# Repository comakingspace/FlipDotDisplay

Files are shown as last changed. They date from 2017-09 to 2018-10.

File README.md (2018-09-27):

# FlipDotDisplay
3 old flip dot displays which need some work to get up and running.

They were bought at the Makerfaire Hannover 2016.

Hardware design is made in KiCAD 4.

## Function

A dot on the display is switched by magnetising an inductor, which causes the colored dot (with a small magnet embedded) to change the orientation. Because the core of the inductor stays magnetized the state of the dot is stable even without being powered.

The inductors of the pixels are hooked up in an array with 24x16. Each column is connected to a single pin of the connector and each row has two inputs; one for positive voltage and one for negative (see FlipDotSchematic). By applying a voltage to a row and a column the corresponding pixel is flipped depending on the current flow direction. The original driver probably used two different power rails and sets of transistors to change the direction of the dot. 

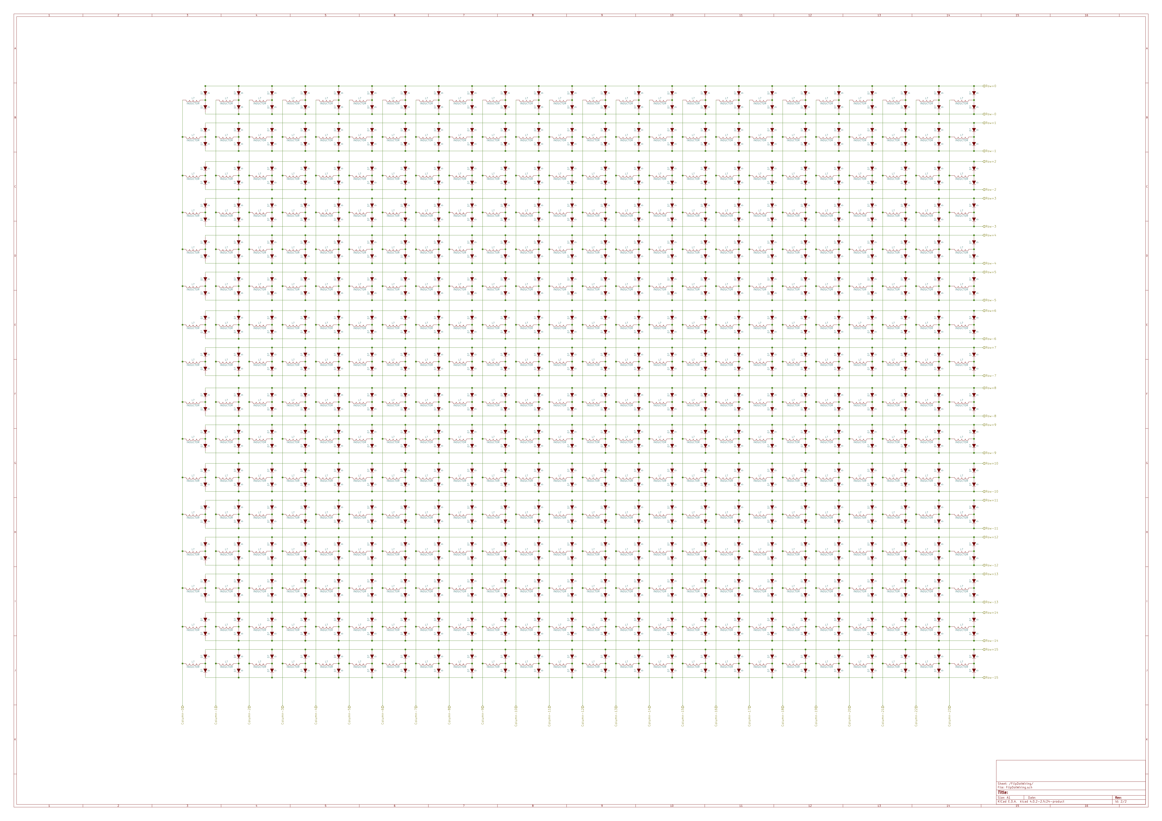
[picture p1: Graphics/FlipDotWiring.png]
Schematic of the FlipDotDisplay


The new driver will use a half-bridge configuration on each input to select the current flow direction. 

## ICs

* Half-bridge driver ICs: **L293D**
* Shift registers for output : **SN74HC595**
* Controller: **Atmega328p** (communicates via serial with the ESP8266)
* Interface for network: ESP8266 (Wemos D1 mini)

## Features

* [Adafruit GFX library](https://github.com/adafruit/Adafruit-GFX-Library) implementation
* MQTT string scroll text

## ToDo

* Pull tweets and display them (direct Hex code or text)
* Binary via MQTT
* more ?

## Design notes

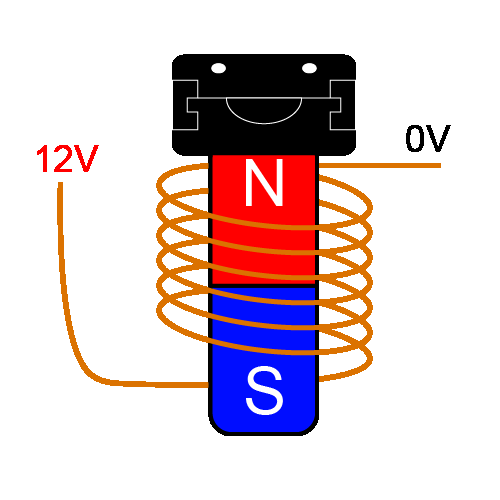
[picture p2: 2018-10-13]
Graphics/FDD_Function.gif

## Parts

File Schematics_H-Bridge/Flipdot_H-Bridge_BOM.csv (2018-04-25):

Id | Designator | Package | Quantity | Designation | Supplier and ref
1 | REF**,REF**,REF**,REF**,REF**,REF**,REF**,REF**,REF**,REF**,REF**,REF**,REF**,REF**,REF**,REF**,REF**,REF**,REF**,REF**,REF** | VIA-0.6mm | 21 | VIA-0.6mm
2 | SW1 | SW_PUSH_6mm | 1 | SW_Push
3 | P3,P2 | Pin_Header_Straight_2x08_Pitch2.54mm | 2 | CONN_02X08
4 | P1 | Pin_Header_Straight_2x13_Pitch2.54mm | 1 | CONN_02X13
5 | Y1 | Crystal_HC49-4H_Vertical | 1 | Crystal
6 | C8,C5,C1 | C_Disc_D4.7mm_W2.5mm_P5.00mm | 3 | 100nF
7 | P4 | Pin_Header_Straight_2x03_Pitch2.54mm | 1 | CONN_02X03
8 | C7,C6 | C_Disc_D4.7mm_W2.5mm_P5.00mm | 2 | 22p
9 | C2 | CP_Radial_D6.3mm_P2.50mm | 1 | 10uF
10 | D2 | LED_D3.0mm | 1 | Led_Yellow
11 | D3 | LED_D3.0mm | 1 | Led_Red
12 | D1 | LED_D3.0mm | 1 | Led_Green
13 | J1 | BARREL_JACK | 1 | Barrel_Jack
14 | C4 | CP_Radial_D6.3mm_P2.50mm | 1 | 1uF
15 | C3 | C_Disc_D4.7mm_W2.5mm_P5.00mm | 1 | 0.33uF
16 | U1,U2,U7,U8,U13 | DIP-16_W7.62mm_Socket | 5 | 74HC595
17 | U3,U4,U5,U6,U9,U10,U11,U12,U14,U15,U16,U17,U18,U19,U21,U22,U23,U24,U25,U26 | DIP-16_W7.62mm_Socket | 20 | L293D
18 | U28 | DIP-28_W7.62mm_Socket | 1 | ATMEGA328P-PU
19 | U27 | TO-220_Vertical | 1 | L7805
20 | R1 | R_Axial_DIN0204_L3.6mm_D1.6mm_P2.54mm_Vertical | 1 | 1k
21 | R2 | R_Axial_DIN0204_L3.6mm_D1.6mm_P2.54mm_Vertical | 1 | 2k
22 | R3,R4,R5 | R_Axial_DIN0204_L3.6mm_D1.6mm_P2.54mm_Vertical | 3 | 1.5K
23 | R6 | R_Axial_DIN0204_L3.6mm_D1.6mm_P2.54mm_Vertical | 1 | 10k
24 | R7 | R_Axial_DIN0204_L3.6mm_D1.6mm_P2.54mm_Vertical | 1 | 1M
25 | REF** | MountingHole_5.3mm_M5_DIN965 | 1 | MountingHole_5.3mm_M5_DIN965
26 | U20 | ESP8266_D1_Mini_cropped | 1 | ESP8266_D1_Mini
27 | G*** | FDD_Icon | 1 | LOGO

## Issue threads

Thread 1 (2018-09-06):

Special character selection doesn't yet work

Pakue95, 2018-09-06:
https://github.com/comakingspace/FlipDotDisplay/blob/ac73b9dc514dd0b5a6fa421b96d9adefe22393e7/Code/FDD-Common_Room/FDD-Common_Room.ino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

When I tired the code yesterday I got the same results as before with weird characters being displayed in place of äö etc.

NitramLegov, 2018-09-08:
https://github.com/comakingspace/FlipDotDisplay/commit/ef07109a65e885bc6020e12cc33ae8bb8f182b74 fixed this

Closed 2018-09-08.

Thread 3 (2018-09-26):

MQTT message size too short for full binary update

Pakue95, 2018-09-26:
Right now the MQTT doesn't like to send/receive more than 103 bytes. Longer messages get ignores.

NitramLegov, 2018-09-26:
The problem is within the adafruit library:
https://github.com/adafruit/Adafruit_MQTT_Library/blob/master/Adafruit_MQTT.h

It defines the maximum message length :
// how much data we save in a subscription object
// and how many subscriptions we want to be able to track.
#if defined  (__AVR_ATmega32U4__) || defined(__AVR_ATmega328P__)
  #define MAXSUBSCRIPTIONS 5
  #define SUBSCRIPTIONDATALEN 20
#else
  #define MAXSUBSCRIPTIONS 15
  #define SUBSCRIPTIONDATALEN 100
#endif

Unfortunately it is a define and not a variable. Thus, as far as I know we would have to fork the library in order to change the value.

Pakue95, 2018-09-27:
I tried increasing this value, but the limit still is present. Maybe another hard-coded max value somewhere?

Pakue95, 2018-09-27:
Someone else also has that problem. Should be fixed however...

https://github.com/adafruit/Adafruit_MQTT_Library/issues/17

Pakue95, 2018-10-14:
Might be an opportunity to change the development environment from Arduino to Espressif.

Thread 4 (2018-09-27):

BinaryTopic randomly gets triggered

Pakue95, 2018-09-27:
I noticed that the display prints out the last binary image (randomly ?) now and then. Can the MQTT server push old data?

NitramLegov, 2018-09-27:
Hmmm, in general, this should not be the case. Can you check, which QoS you are using when sending the data?
If you use another client and subscribe to the topic # you will get all messages on all topics, so you would see what the server sends.

NitramLegov, 2018-09-28:
The issue is that somebody (not looking at @Narquadah of course :D ) sent a retained message to the broker. Retained messages are explained here:
https://www.hivemq.com/blog/mqtt-essentials-part-8-retained-messages

> "A retained message is a normal MQTT message with the retained flag set to true. The broker stores the last retained message and the corresponding QoS for that topic. Each client that subscribes to a topic pattern that matches the topic of the retained message receives the retained message immediately after they subscribe. The broker stores only one retained message per topic."

In order to solve the issue, I deleted the retained message:

> "There is also a very simple way to delete the retained message of a topic: send a retained message with a zero-byte payload on the topic where you want to delete the previous retained message. The broker deletes the retained message and new subscribers no longer get a retained message for that topic. Frequently, it is not even necessary to delete, because each new retained message overwrites the previous one."

Closed 2018-10-13.

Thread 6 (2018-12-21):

MQTT client looses connection to the Broker

NitramLegov, 2018-12-21:
Unfortunately, the MQTT client looses the connection to the broker regularly.

In the broker log, you can see that the client tries to reconnect, but the broker throws an socket error.
We have two options:
1. change the mqtt library used on the client side (@Narquadah mentioned pubsubclient works for him).
Here we need to ensure the paket sizes can be adjusted. According to https://github.com/knolleary/pubsubclient/issues/110 this should work.
2. Try to debug why there is a socket error.

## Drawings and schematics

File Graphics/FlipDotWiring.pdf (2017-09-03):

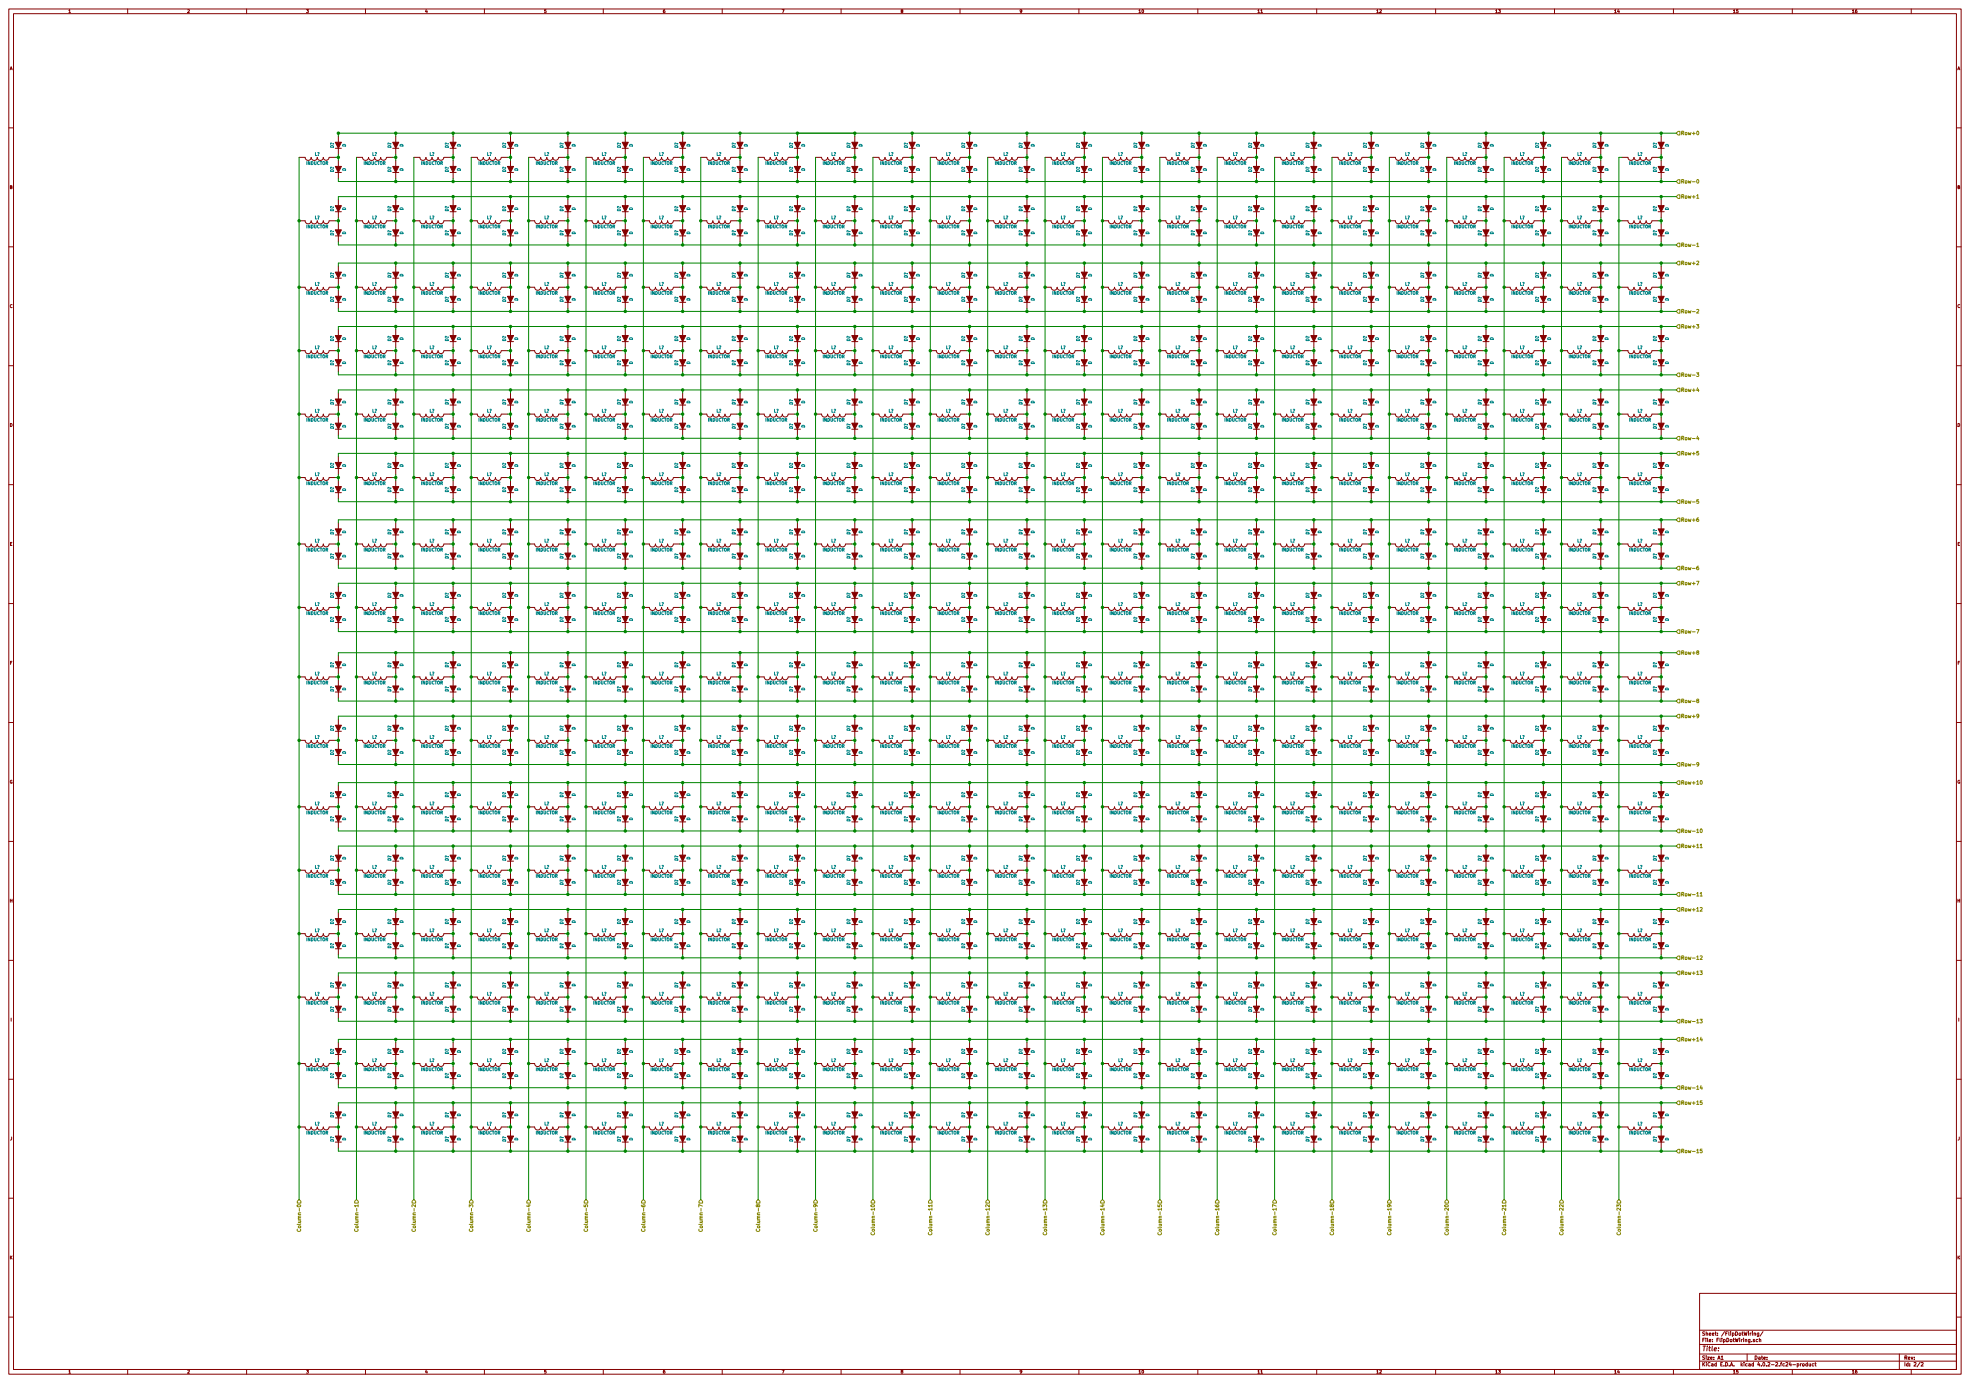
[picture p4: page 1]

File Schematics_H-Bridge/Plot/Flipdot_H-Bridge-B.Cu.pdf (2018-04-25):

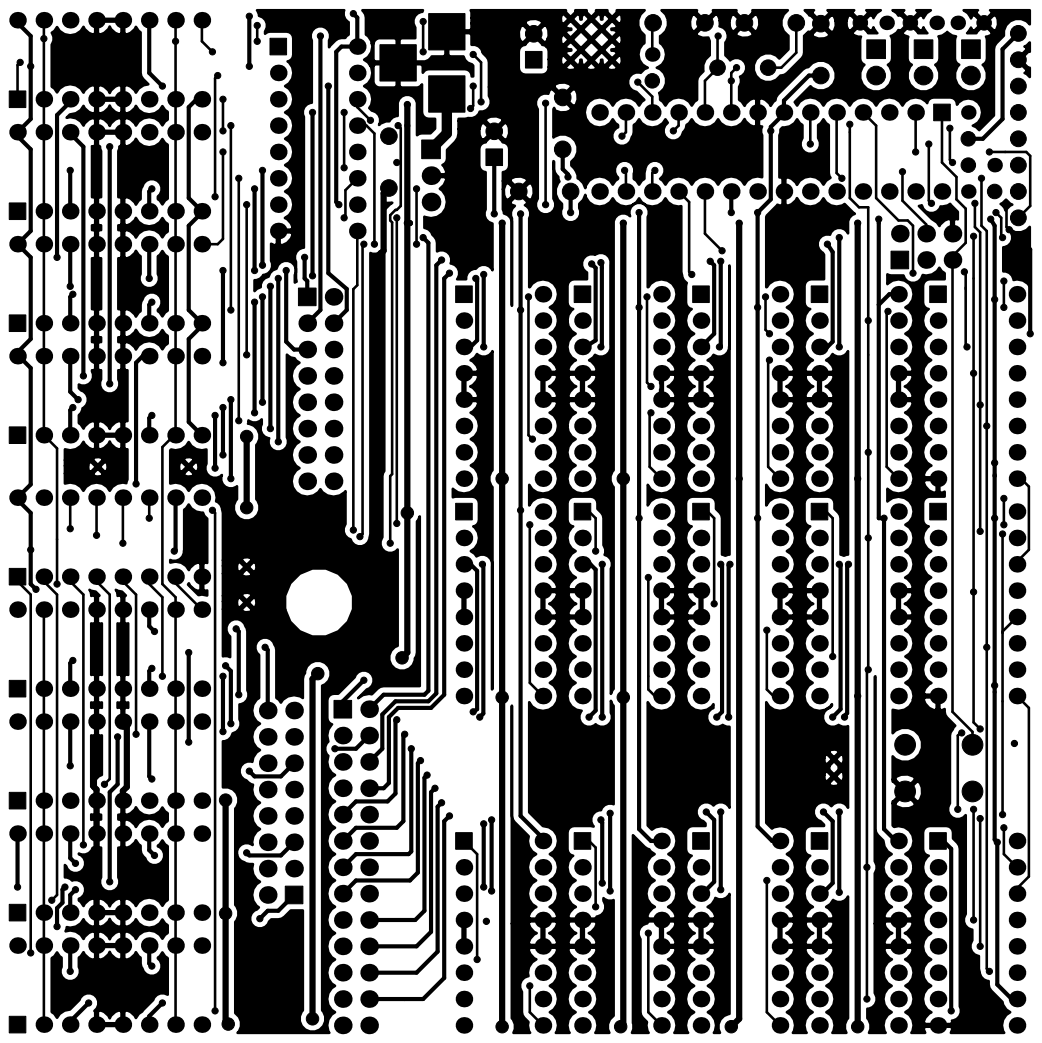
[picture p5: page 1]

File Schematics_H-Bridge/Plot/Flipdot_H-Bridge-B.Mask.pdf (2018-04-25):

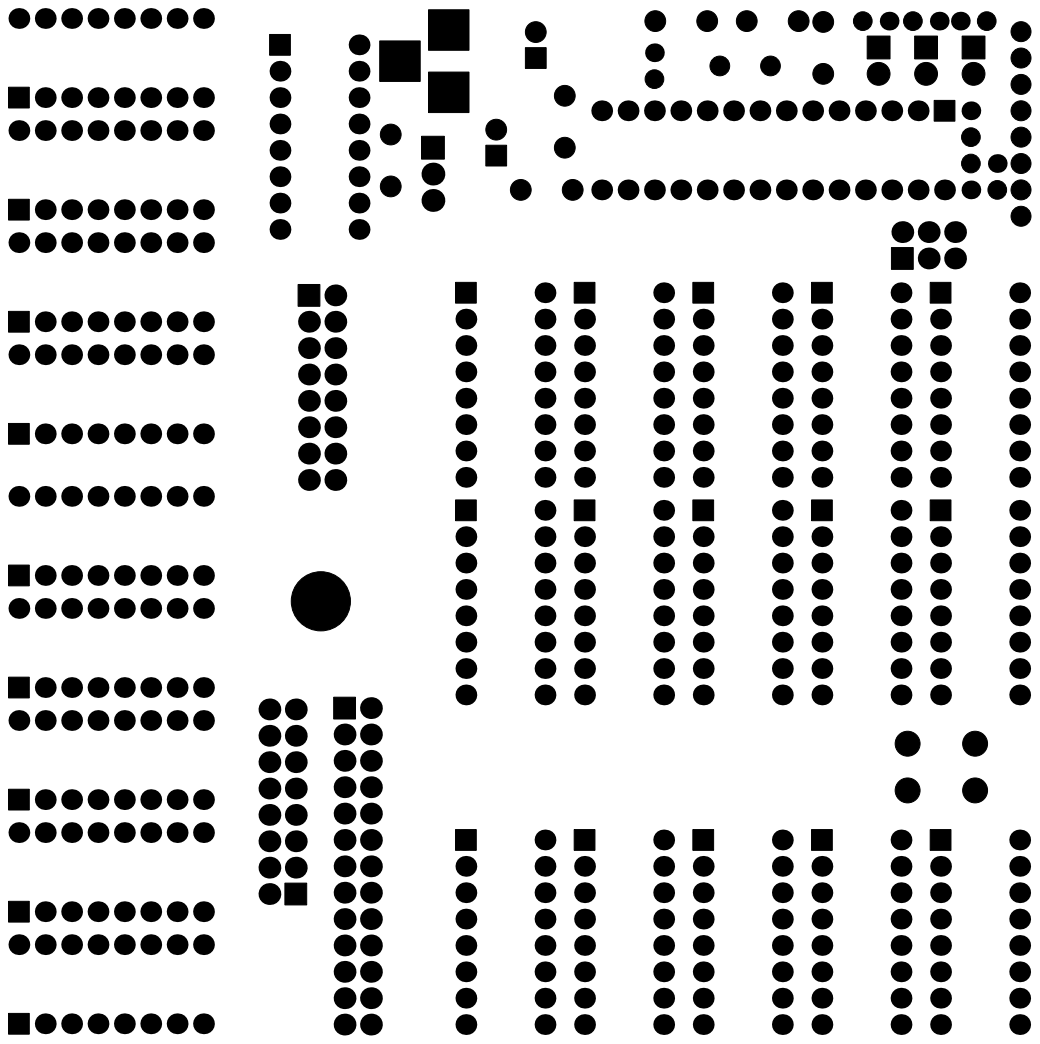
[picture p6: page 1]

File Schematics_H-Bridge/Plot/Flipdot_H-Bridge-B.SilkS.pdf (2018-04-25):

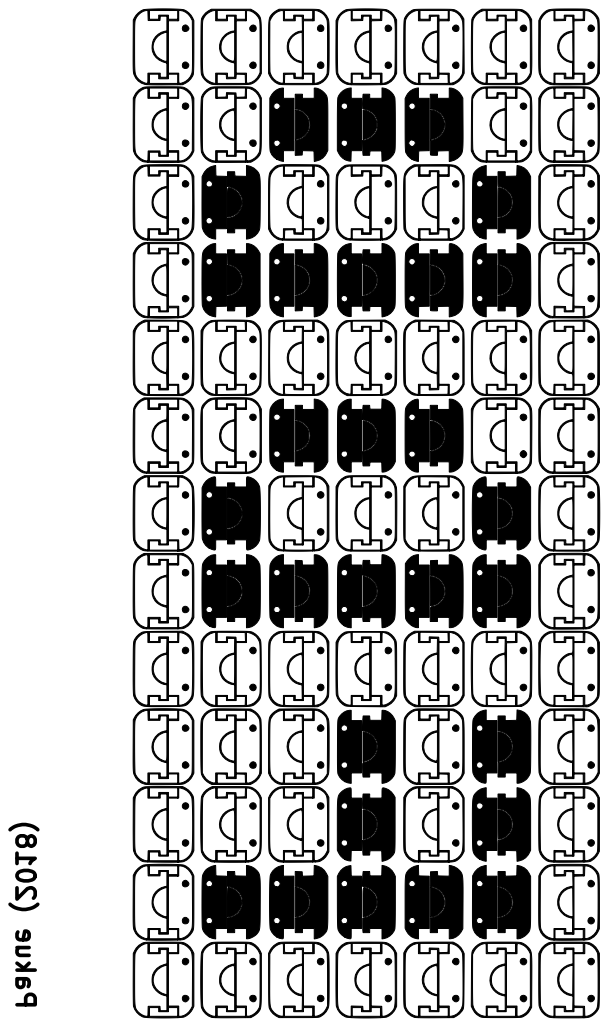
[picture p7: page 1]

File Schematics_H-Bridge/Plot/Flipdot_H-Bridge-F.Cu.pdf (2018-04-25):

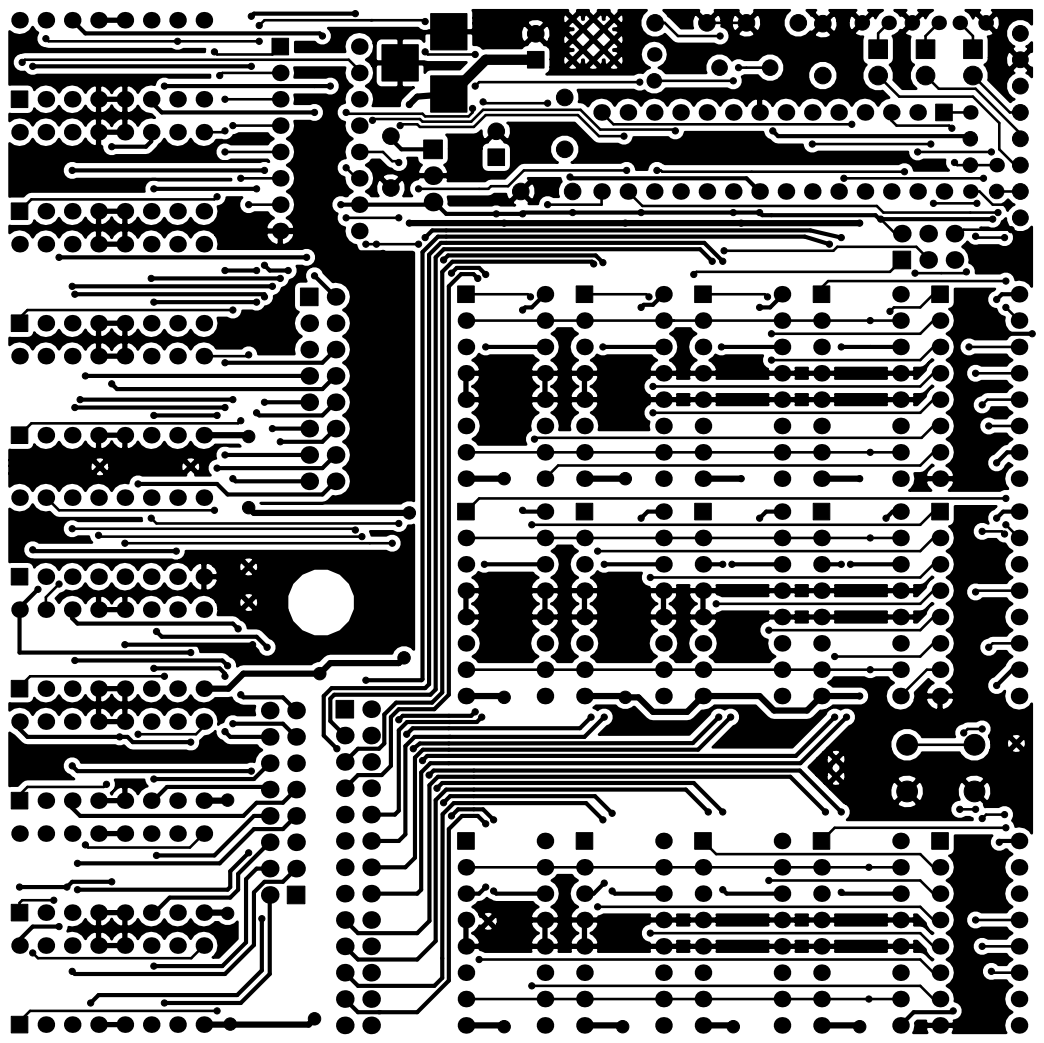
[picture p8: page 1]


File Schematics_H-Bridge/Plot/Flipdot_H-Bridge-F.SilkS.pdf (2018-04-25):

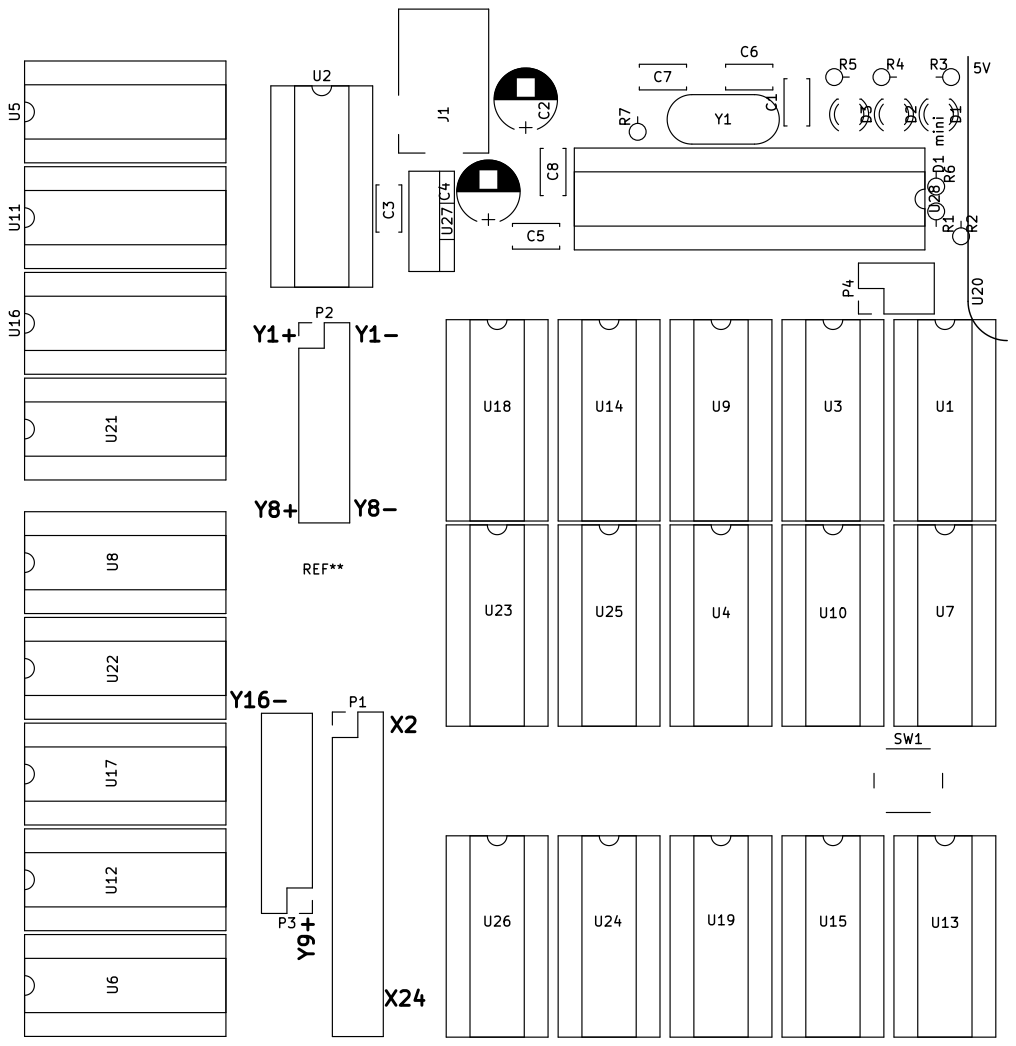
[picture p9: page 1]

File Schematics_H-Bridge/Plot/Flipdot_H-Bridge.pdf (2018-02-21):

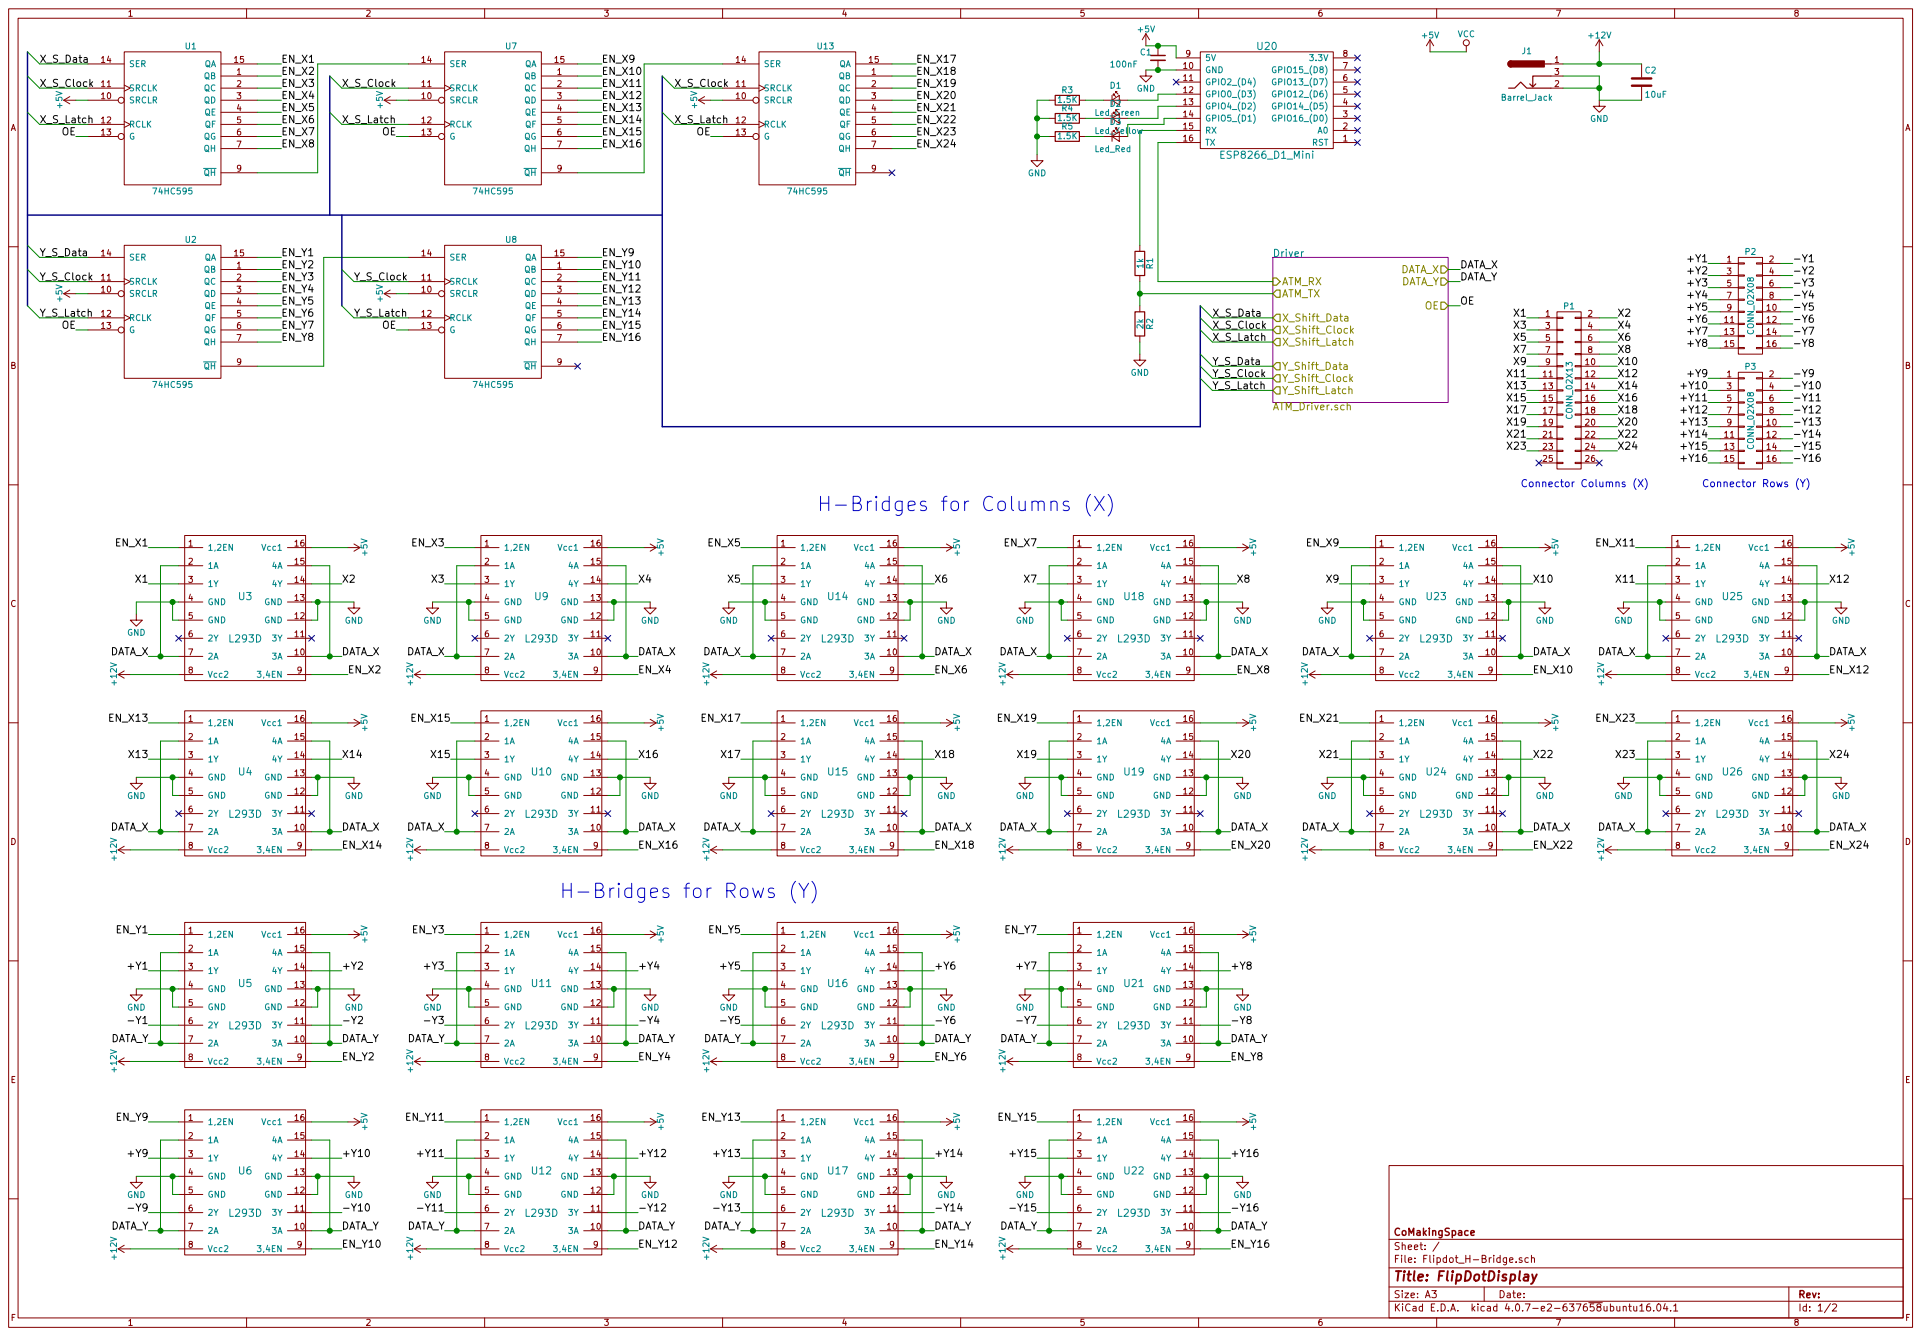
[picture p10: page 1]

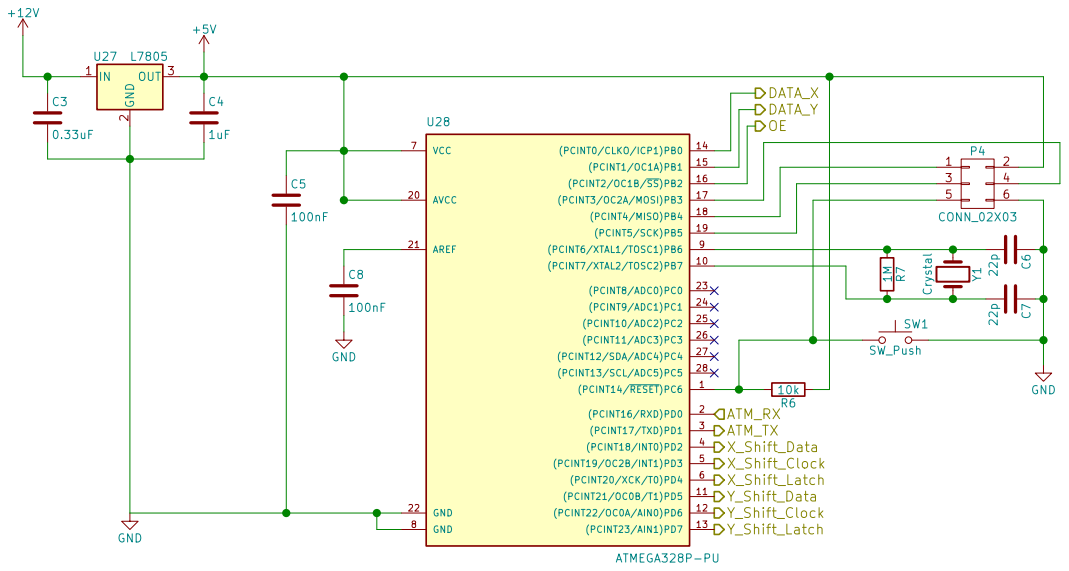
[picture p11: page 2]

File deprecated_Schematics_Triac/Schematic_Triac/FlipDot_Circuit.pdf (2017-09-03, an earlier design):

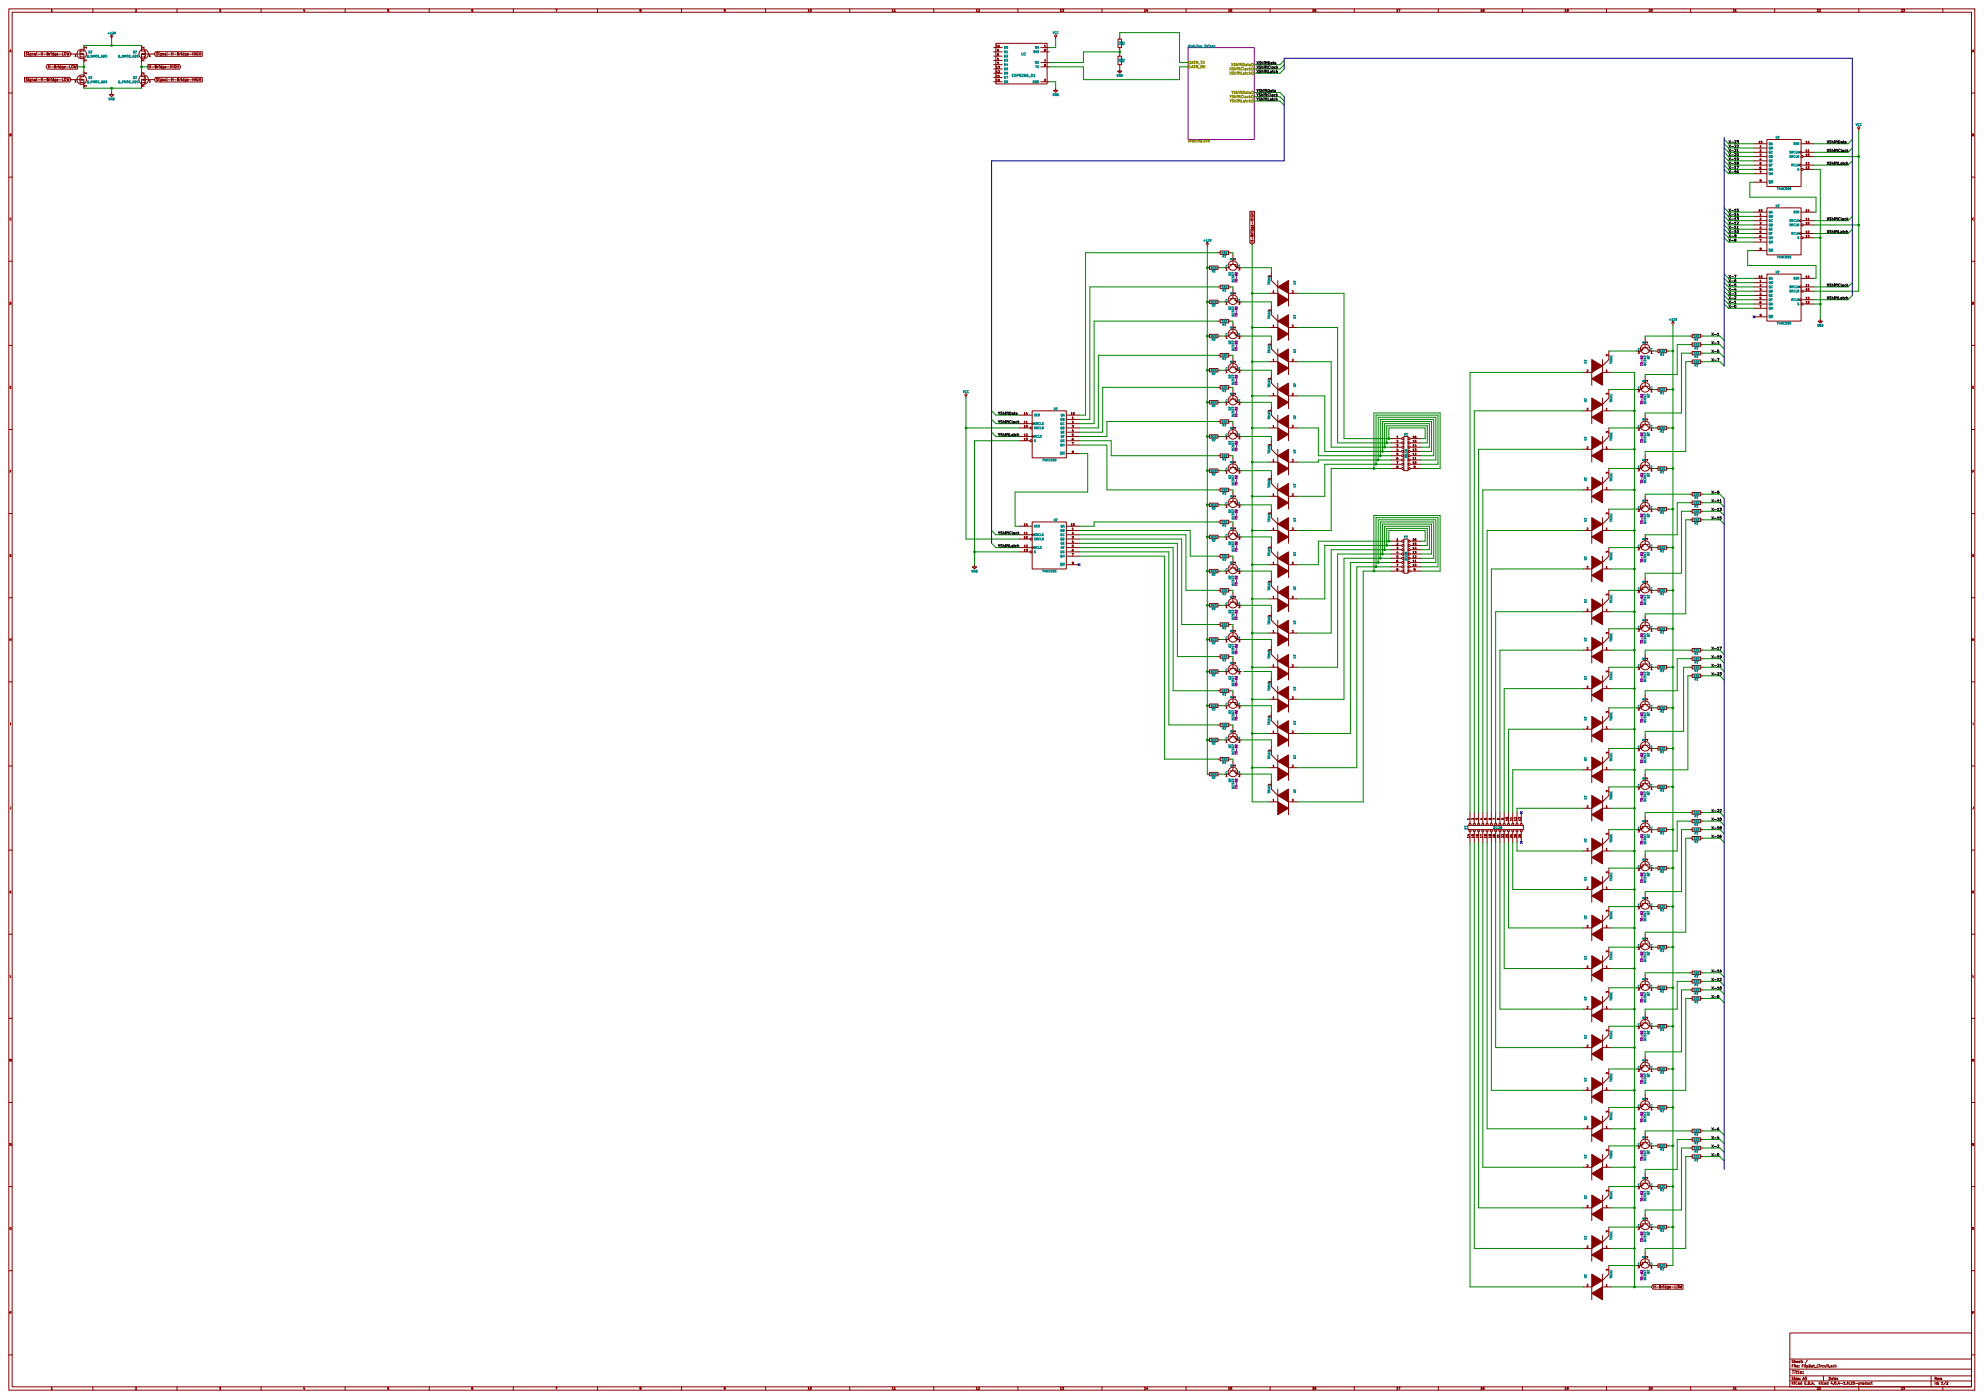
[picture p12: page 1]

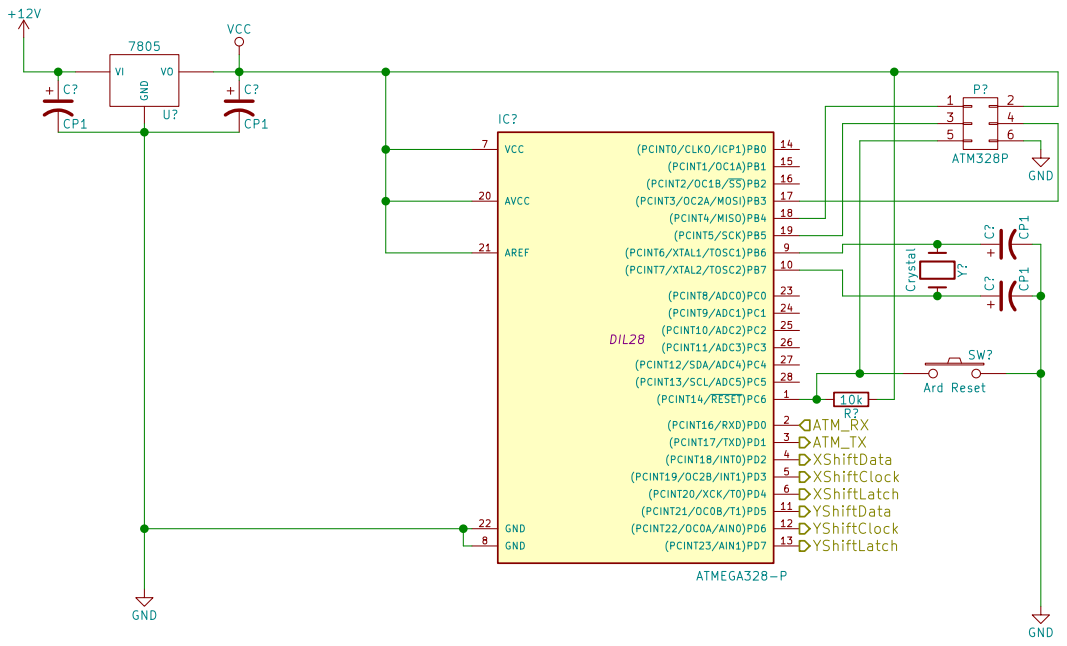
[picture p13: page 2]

Id: 2/2 Title: File: Arduino.sch Sheet: /Arduino_Driver/

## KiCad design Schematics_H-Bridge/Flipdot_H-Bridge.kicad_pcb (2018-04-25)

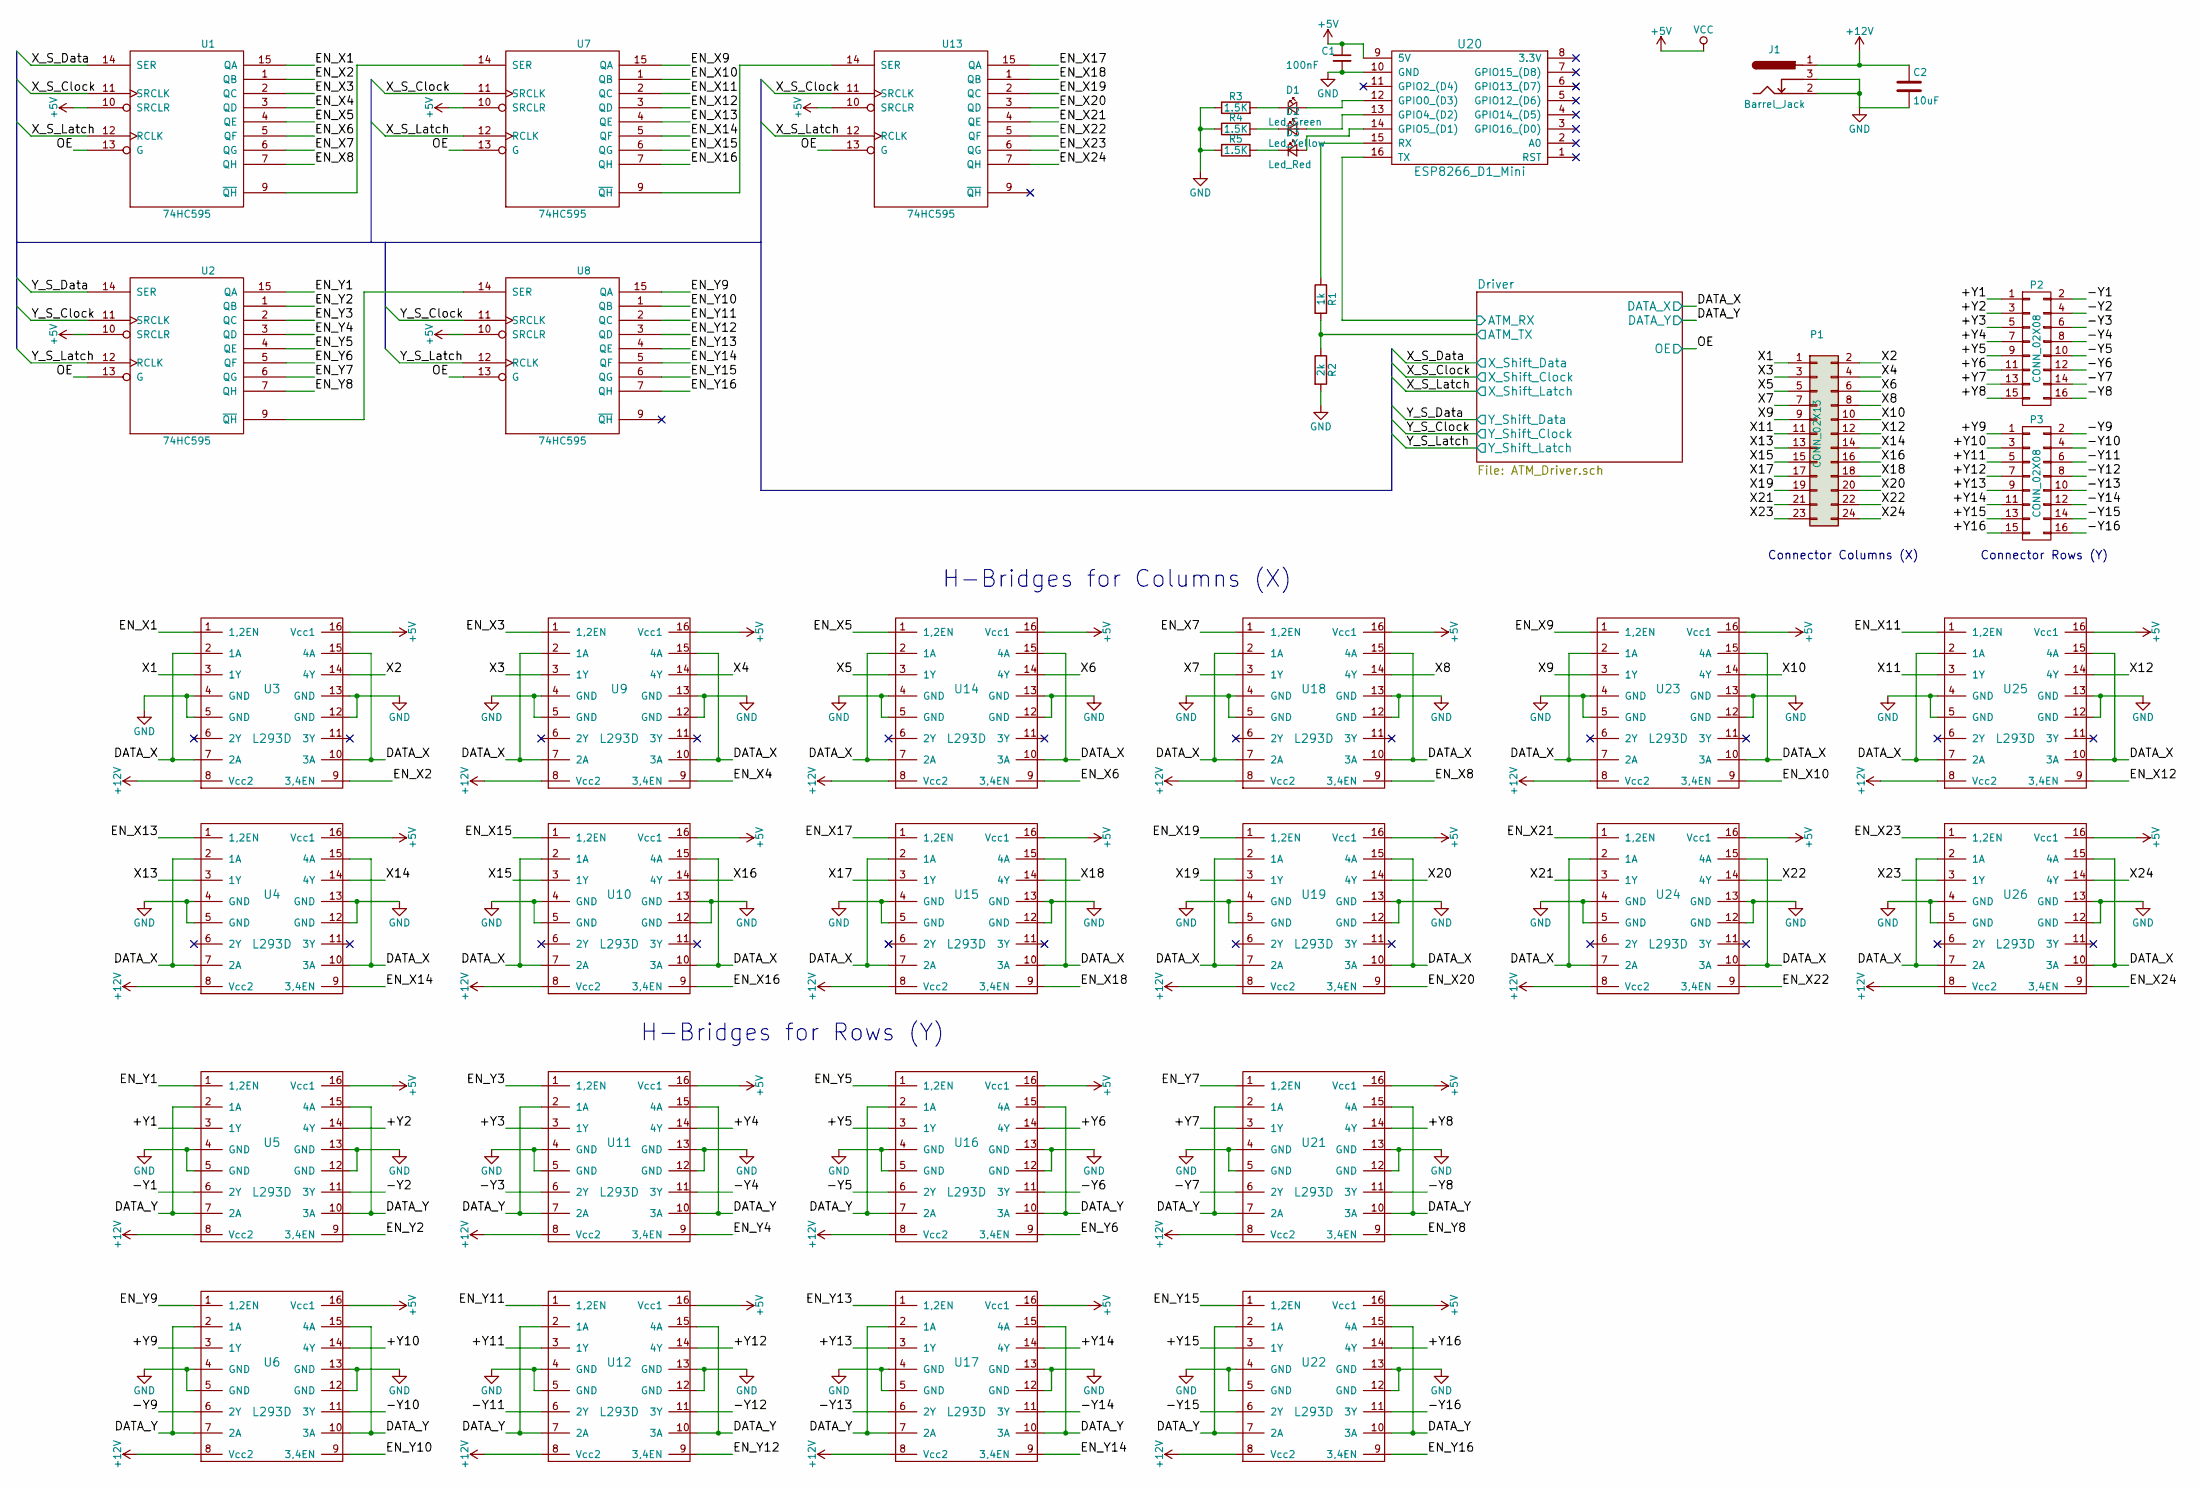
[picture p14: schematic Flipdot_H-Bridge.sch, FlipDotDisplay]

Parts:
C1: 100nF; C_Disc_D4.7mm_W2.5mm_P5.00mm
C2: 10uF; CP_Radial_D6.3mm_P2.50mm
D1: Led_Green; LED_D3.0mm
D2: Led_Yellow; LED_D3.0mm
D3: Led_Red; LED_D3.0mm
J1: Barrel_Jack; BARREL_JACK
P1: CONN_02X13; Pin_Header_Straight_2x13_Pitch2.54mm
P2, P3: CONN_02X08; Pin_Header_Straight_2x08_Pitch2.54mm
R1: 1k; R_Axial_DIN0204_L3.6mm_D1.6mm_P2.54mm_Vertical
R2: 2k; R_Axial_DIN0204_L3.6mm_D1.6mm_P2.54mm_Vertical
R3, R4, R5: 1.5K; R_Axial_DIN0204_L3.6mm_D1.6mm_P2.54mm_Vertical
U1, U2, U7, U8, U13: 74HC595; DIP-16_W7.62mm_Socket
U3, U4, U5, U6, U9, U10, U11, U12, U14, U15, U16, U17, U18, U19, U21, U22, U23, U24, U25, U26: L293D; DIP-16_W7.62mm_Socket
U20: ESP8266_D1_Mini

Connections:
+5V: C1.1, U1.10 (SRCLR), U1.16 (VCC), U2.10 (SRCLR), U2.16 (VCC), U3.16 (Vcc1), U4.16 (Vcc1), U5.16 (Vcc1), U6.16 (Vcc1), U7.10 (SRCLR), U7.16 (VCC), U8.10 (SRCLR), U8.16 (VCC), U9.16 (Vcc1), U10.16 (Vcc1), U11.16 (Vcc1), U12.16 (Vcc1), U13.10 (SRCLR), U13.16 (VCC), U14.16 (Vcc1), U15.16 (Vcc1), U16.16 (Vcc1), U17.16 (Vcc1), U18.16 (Vcc1), U19.16 (Vcc1), U20.9 (5V), U21.16 (Vcc1), U22.16 (Vcc1), U23.16 (Vcc1), U24.16 (Vcc1), U25.16 (Vcc1), U26.16 (Vcc1); also elsewhere on the board
+12V: C2.1, J1.1, U3.8 (Vcc2), U4.8 (Vcc2), U5.8 (Vcc2), U6.8 (Vcc2), U9.8 (Vcc2), U10.8 (Vcc2), U11.8 (Vcc2), U12.8 (Vcc2), U14.8 (Vcc2), U15.8 (Vcc2), U16.8 (Vcc2), U17.8 (Vcc2), U18.8 (Vcc2), U19.8 (Vcc2), U21.8 (Vcc2), U22.8 (Vcc2), U23.8 (Vcc2), U24.8 (Vcc2), U25.8 (Vcc2), U26.8 (Vcc2); also elsewhere on the board
/+Y1: P2.1, U5.3 (1Y)
/+Y2: P2.3, U5.14 (4Y)
/+Y3: P2.5, U11.3 (1Y)
/+Y4: P2.7, U11.14 (4Y)
/+Y5: P2.9, U16.3 (1Y)
/+Y6: P2.11, U16.14 (4Y)
/+Y7: P2.13, U21.3 (1Y)
/+Y8: P2.15, U21.14 (4Y)
/+Y9: P3.1, U6.3 (1Y)
/+Y10: P3.3, U6.14 (4Y)
/+Y11: P3.5, U12.3 (1Y)
/+Y12: P3.7, U12.14 (4Y)
/+Y13: P3.9, U17.3 (1Y)
/+Y14: P3.11, U17.14 (4Y)
/+Y15: P3.13, U22.3 (1Y)
/+Y16: P3.15, U22.14 (4Y)
/-Y1: P2.2, U5.6 (2Y)
/-Y2: P2.4, U5.11 (3Y)
/-Y3: P2.6, U11.6 (2Y)
/-Y4: P2.8, U11.11 (3Y)
/-Y5: P2.10, U16.6 (2Y)
/-Y6: P2.12, U16.11 (3Y)
/-Y7: P2.14, U21.6 (2Y)
/-Y8: P2.16, U21.11 (3Y)
/-Y9: P3.2, U6.6 (2Y)
/-Y10: P3.4, U6.11 (3Y)
/-Y11: P3.6, U12.6 (2Y)
/-Y12: P3.8, U12.11 (3Y)
/-Y13: P3.10, U17.6 (2Y)
/-Y14: P3.12, U17.11 (3Y)
/-Y15: P3.14, U22.6 (2Y)
/-Y16: P3.16, U22.11 (3Y)
/DATA_X: U3.2 (1A), U3.7 (2A), U3.10 (3A), U3.15 (4A), U4.2 (1A), U4.7 (2A), U4.10 (3A), U4.15 (4A), U9.2 (1A), U9.7 (2A), U9.10 (3A), U9.15 (4A), U10.2 (1A), U10.7 (2A), U10.10 (3A), U10.15 (4A), U14.2 (1A), U14.7 (2A), U14.10 (3A), U14.15 (4A), U15.2 (1A), U15.7 (2A), U15.10 (3A), U15.15 (4A), U18.2 (1A), U18.7 (2A), U18.10 (3A), U18.15 (4A), U19.2 (1A), U19.7 (2A), U19.10 (3A), U19.15 (4A), U23.2 (1A), U23.7 (2A), U23.10 (3A), U23.15 (4A), U24.2 (1A), U24.7 (2A), U24.10 (3A), U24.15 (4A), U25.2 (1A), U25.7 (2A), U25.10 (3A), U25.15 (4A), U26.2 (1A), U26.7 (2A), U26.10 (3A), U26.15 (4A); also elsewhere on the board
/DATA_Y: U5.2 (1A), U5.7 (2A), U5.10 (3A), U5.15 (4A), U6.2 (1A), U6.7 (2A), U6.10 (3A), U6.15 (4A), U11.2 (1A), U11.7 (2A), U11.10 (3A), U11.15 (4A), U12.2 (1A), U12.7 (2A), U12.10 (3A), U12.15 (4A), U16.2 (1A), U16.7 (2A), U16.10 (3A), U16.15 (4A), U17.2 (1A), U17.7 (2A), U17.10 (3A), U17.15 (4A), U21.2 (1A), U21.7 (2A), U21.10 (3A), U21.15 (4A), U22.2 (1A), U22.7 (2A), U22.10 (3A), U22.15 (4A); also elsewhere on the board
/Driver/ATM_RX: U20.16 (TX); also elsewhere on the board
/Driver/ATM_TX: R1.2, R2.1; also elsewhere on the board
/EN_X1: U1.15 (QA), U3.1 (1,2EN)
/EN_X2: U1.1 (QB), U3.9 (3,4EN)
/EN_X3: U1.2 (QC), U9.1 (1,2EN)
/EN_X4: U1.3 (QD), U9.9 (3,4EN)
/EN_X5: U1.4 (QE), U14.1 (1,2EN)
/EN_X6: U1.5 (QF), U14.9 (3,4EN)
/EN_X7: U1.6 (QG), U18.1 (1,2EN)
/EN_X8: U1.7 (QH), U18.9 (3,4EN)
/EN_X9: U7.15 (QA), U23.1 (1,2EN)
/EN_X10: U7.1 (QB), U23.9 (3,4EN)
/EN_X11: U7.2 (QC), U25.1 (1,2EN)
/EN_X12: U7.3 (QD), U25.9 (3,4EN)
/EN_X13: U4.1 (1,2EN), U7.4 (QE)
/EN_X14: U4.9 (3,4EN), U7.5 (QF)
/EN_X15: U7.6 (QG), U10.1 (1,2EN)
/EN_X16: U7.7 (QH), U10.9 (3,4EN)
/EN_X17: U13.15 (QA), U15.1 (1,2EN)
/EN_X18: U13.1 (QB), U15.9 (3,4EN)
/EN_X19: U13.2 (QC), U19.1 (1,2EN)
/EN_X20: U13.3 (QD), U19.9 (3,4EN)
/EN_X21: U13.4 (QE), U24.1 (1,2EN)
/EN_X22: U13.5 (QF), U24.9 (3,4EN)
/EN_X23: U13.6 (QG), U26.1 (1,2EN)
/EN_X24: U13.7 (QH), U26.9 (3,4EN)
/EN_Y1: U2.15 (QA), U5.1 (1,2EN)
/EN_Y2: U2.1 (QB), U5.9 (3,4EN)
/EN_Y3: U2.2 (QC), U11.1 (1,2EN)
/EN_Y4: U2.3 (QD), U11.9 (3,4EN)
/EN_Y5: U2.4 (QE), U16.1 (1,2EN)
/EN_Y6: U2.5 (QF), U16.9 (3,4EN)
/EN_Y7: U2.6 (QG), U21.1 (1,2EN)
/EN_Y8: U2.7 (QH), U21.9 (3,4EN)
/EN_Y9: U6.1 (1,2EN), U8.15 (QA)
/EN_Y10: U6.9 (3,4EN), U8.1 (QB)
/EN_Y11: U8.2 (QC), U12.1 (1,2EN)
/EN_Y12: U8.3 (QD), U12.9 (3,4EN)
/EN_Y13: U8.4 (QE), U17.1 (1,2EN)
/EN_Y14: U8.5 (QF), U17.9 (3,4EN)
/EN_Y15: U8.6 (QG), U22.1 (1,2EN)
/EN_Y16: U8.7 (QH), U22.9 (3,4EN)
/OE: U1.13 (G), U2.13 (G), U7.13 (G), U8.13 (G), U13.13 (G); also elsewhere on the board
/X1: P1.1, U3.3 (1Y)
/X2: P1.2, U3.14 (4Y)
/X3: P1.3, U9.3 (1Y)
/X4: P1.4, U9.14 (4Y)
/X5: P1.5, U14.3 (1Y)
/X6: P1.6, U14.14 (4Y)
/X7: P1.7, U18.3 (1Y)
/X8: P1.8, U18.14 (4Y)
/X9: P1.9, U23.3 (1Y)
/X10: P1.10, U23.14 (4Y)
/X11: P1.11, U25.3 (1Y)
/X12: P1.12, U25.14 (4Y)
/X13: P1.13, U4.3 (1Y)
/X14: P1.14, U4.14 (4Y)
/X15: P1.15, U10.3 (1Y)
/X16: P1.16, U10.14 (4Y)
/X17: P1.17, U15.3 (1Y)
/X18: P1.18, U15.14 (4Y)
/X19: P1.19, U19.3 (1Y)
/X20: P1.20, U19.14 (4Y)
/X21: P1.21, U24.3 (1Y)
/X22: P1.22, U24.14 (4Y)
/X23: P1.23, U26.3 (1Y)
/X24: P1.24, U26.14 (4Y)
/X_S_Clock: U1.11 (SRCLK), U7.11 (SRCLK), U13.11 (SRCLK); also elsewhere on the board
/X_S_Data: U1.14 (SER); also elsewhere on the board
/X_S_Latch: U1.12 (RCLK), U7.12 (RCLK), U13.12 (RCLK); also elsewhere on the board
/Y_S_Clock: U2.11 (SRCLK), U8.11 (SRCLK); also elsewhere on the board
/Y_S_Data: U2.14 (SER); also elsewhere on the board
/Y_S_Latch: U2.12 (RCLK), U8.12 (RCLK); also elsewhere on the board
GND: C1.2, C2.2, J1.2, J1.3, R2.2, R3.1, R4.1, R5.1, U1.8 (GND), U2.8 (GND), U3.4 (GND), U3.5 (GND), U3.12 (GND), U3.13 (GND), U4.4 (GND), U4.5 (GND), U4.12 (GND), U4.13 (GND), U5.4 (GND), U5.5 (GND), U5.12 (GND), U5.13 (GND), U6.4 (GND), U6.5 (GND), U6.12 (GND), U6.13 (GND), U7.8 (GND), U8.8 (GND), U9.4 (GND), U9.5 (GND), U9.12 (GND), U9.13 (GND), U10.4 (GND), U10.5 (GND), U10.12 (GND), U10.13 (GND), U11.4 (GND), U11.5 (GND), U11.12 (GND), U11.13 (GND), U12.4 (GND), U12.5 (GND), U12.12 (GND), U12.13 (GND), U13.8 (GND), U14.4 (GND), U14.5 (GND), U14.12 (GND), U14.13 (GND), U15.4 (GND), U15.5 (GND), U15.12 (GND), U15.13 (GND), U16.4 (GND), U16.5 (GND), U16.12 (GND), U16.13 (GND), U17.4 (GND), U17.5 (GND), U17.12 (GND), U17.13 (GND), U18.4 (GND), U18.5 (GND), U18.12 (GND), U18.13 (GND), U19.4 (GND), U19.5 (GND), U19.12 (GND), U19.13 (GND), U20.10 (GND), U21.4 (GND), U21.5 (GND), U21.12 (GND), U21.13 (GND), U22.4 (GND), U22.5 (GND), U22.12 (GND), U22.13 (GND), U23.4 (GND), U23.5 (GND), U23.12 (GND), U23.13 (GND), U24.4 (GND), U24.5 (GND), U24.12 (GND), U24.13 (GND), U25.4 (GND), U25.5 (GND), U25.12 (GND), U25.13 (GND), U26.4 (GND), U26.5 (GND), U26.12 (GND), U26.13 (GND); also elsewhere on the board
unnamed: D1.1 (K), R3.2
unnamed: D1.2 (A), U20.12 (GPIO0_(D3))
unnamed: D2.1 (K), R4.2
unnamed: D2.2 (A), U20.13 (GPIO4_(D2))
unnamed: D3.1 (K), R5.2
unnamed: D3.2 (A), U20.14 (GPIO5_(D1))
unnamed: R1.1, U20.15 (RX)
unnamed: U1.9 (~QH), U7.14 (SER)
unnamed: U2.9 (~QH), U8.14 (SER)
unnamed: U7.9 (~QH), U13.14 (SER)

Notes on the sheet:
Connector Columns (X)
Connector Rows (Y)
H-Bridges for Rows (Y)
H-Bridges for Columns (X)

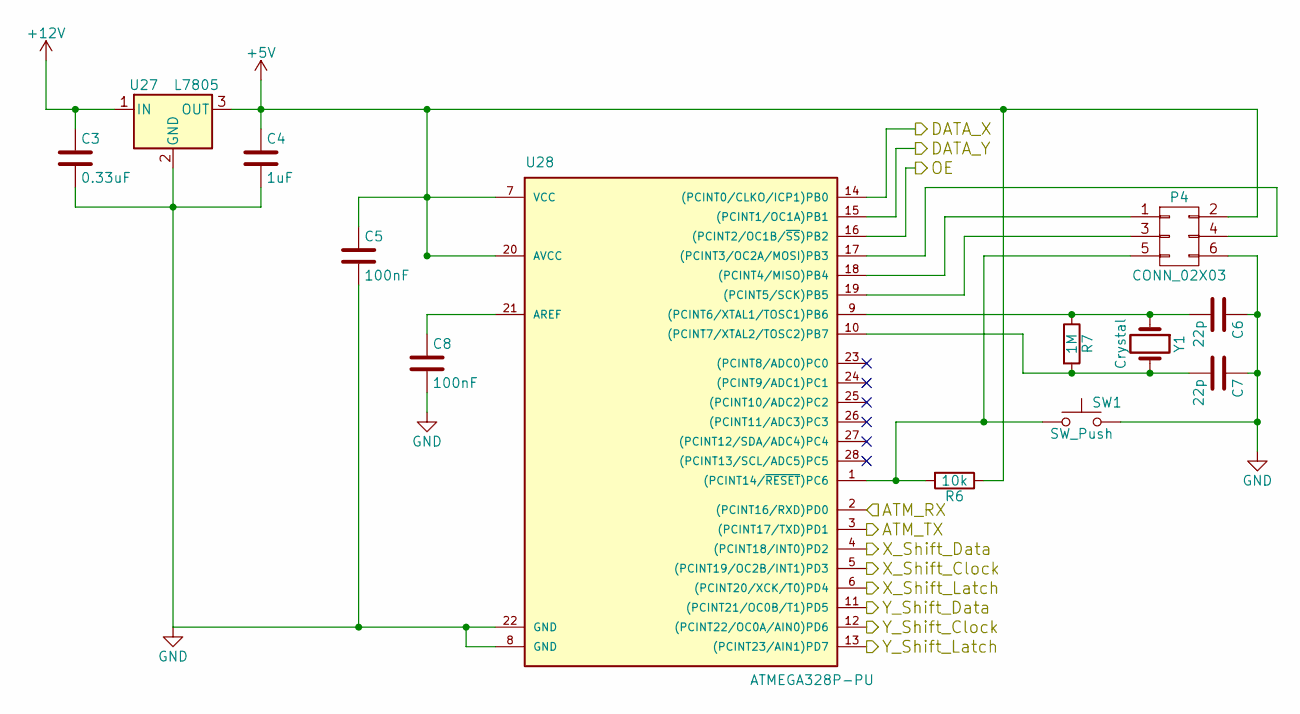
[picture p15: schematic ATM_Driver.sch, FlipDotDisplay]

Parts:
C3: 0.33uF; C_Disc_D4.7mm_W2.5mm_P5.00mm
C4: 1uF; CP_Radial_D6.3mm_P2.50mm
C5, C8: 100nF; C_Disc_D4.7mm_W2.5mm_P5.00mm
C6, C7: 22p; C_Disc_D4.7mm_W2.5mm_P5.00mm
P4: CONN_02X03; Pin_Header_Straight_2x03_Pitch2.54mm
R6: 10k; R_Axial_DIN0204_L3.6mm_D1.6mm_P2.54mm_Vertical
R7: 1M; R_Axial_DIN0204_L3.6mm_D1.6mm_P2.54mm_Vertical
SW1: SW_Push; SW_PUSH_6mm
U27: L7805; TO-220_Vertical
U28: ATMEGA328P-PU; DIP-28_W7.62mm_Socket
Y1: Crystal; Crystal_HC49-4H_Vertical

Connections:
+5V: C4.1, C5.1, P4.2, R6.1, U27.3 (OUT), U28.7 (VCC), U28.20 (AVCC); also elsewhere on the board
+12V: C3.1, U27.1 (IN); also elsewhere on the board
/DATA_X: U28.14 ((PCINT0/CLKO/ICP1)PB0); also elsewhere on the board
/DATA_Y: U28.15 ((PCINT1/OC1A)PB1); also elsewhere on the board
/Driver/ATM_RX: U28.2 ((PCINT16/RXD)PD0); also elsewhere on the board
/Driver/ATM_TX: U28.3 ((PCINT17/TXD)PD1); also elsewhere on the board
/OE: U28.16 ((PCINT2/OC1B/~SS~)PB2); also elsewhere on the board
/X_S_Clock: U28.5 ((PCINT19/OC2B/INT1)PD3); also elsewhere on the board
/X_S_Data: U28.4 ((PCINT18/INT0)PD2); also elsewhere on the board
/X_S_Latch: U28.6 ((PCINT20/XCK/T0)PD4); also elsewhere on the board
/Y_S_Clock: U28.12 ((PCINT22/OC0A/AIN0)PD6); also elsewhere on the board
/Y_S_Data: U28.11 ((PCINT21/OC0B/T1)PD5); also elsewhere on the board
/Y_S_Latch: U28.13 ((PCINT23/AIN1)PD7); also elsewhere on the board
GND: C3.2, C4.2, C5.2, C6.1, C7.1, C8.2, P4.6, SW1.2, U27.2 (GND), U28.8 (GND), U28.22 (GND); also elsewhere on the board
unnamed: C6.2, R7.1, U28.9 ((PCINT6/XTAL1/TOSC1)PB6), Y1.1
unnamed: C7.2, R7.2, U28.10 ((PCINT7/XTAL2/TOSC2)PB7), Y1.2
unnamed: C8.1, U28.21 (AREF)
unnamed: P4.1, U28.18 ((PCINT4/MISO)PB4)
unnamed: P4.3, U28.19 ((PCINT5/SCK)PB5)
unnamed: P4.4, U28.17 ((PCINT3/OC2A/MOSI)PB3)
unnamed: P4.5, R6.2, SW1.1, U28.1 ((PCINT14/~RESET~)PC6)

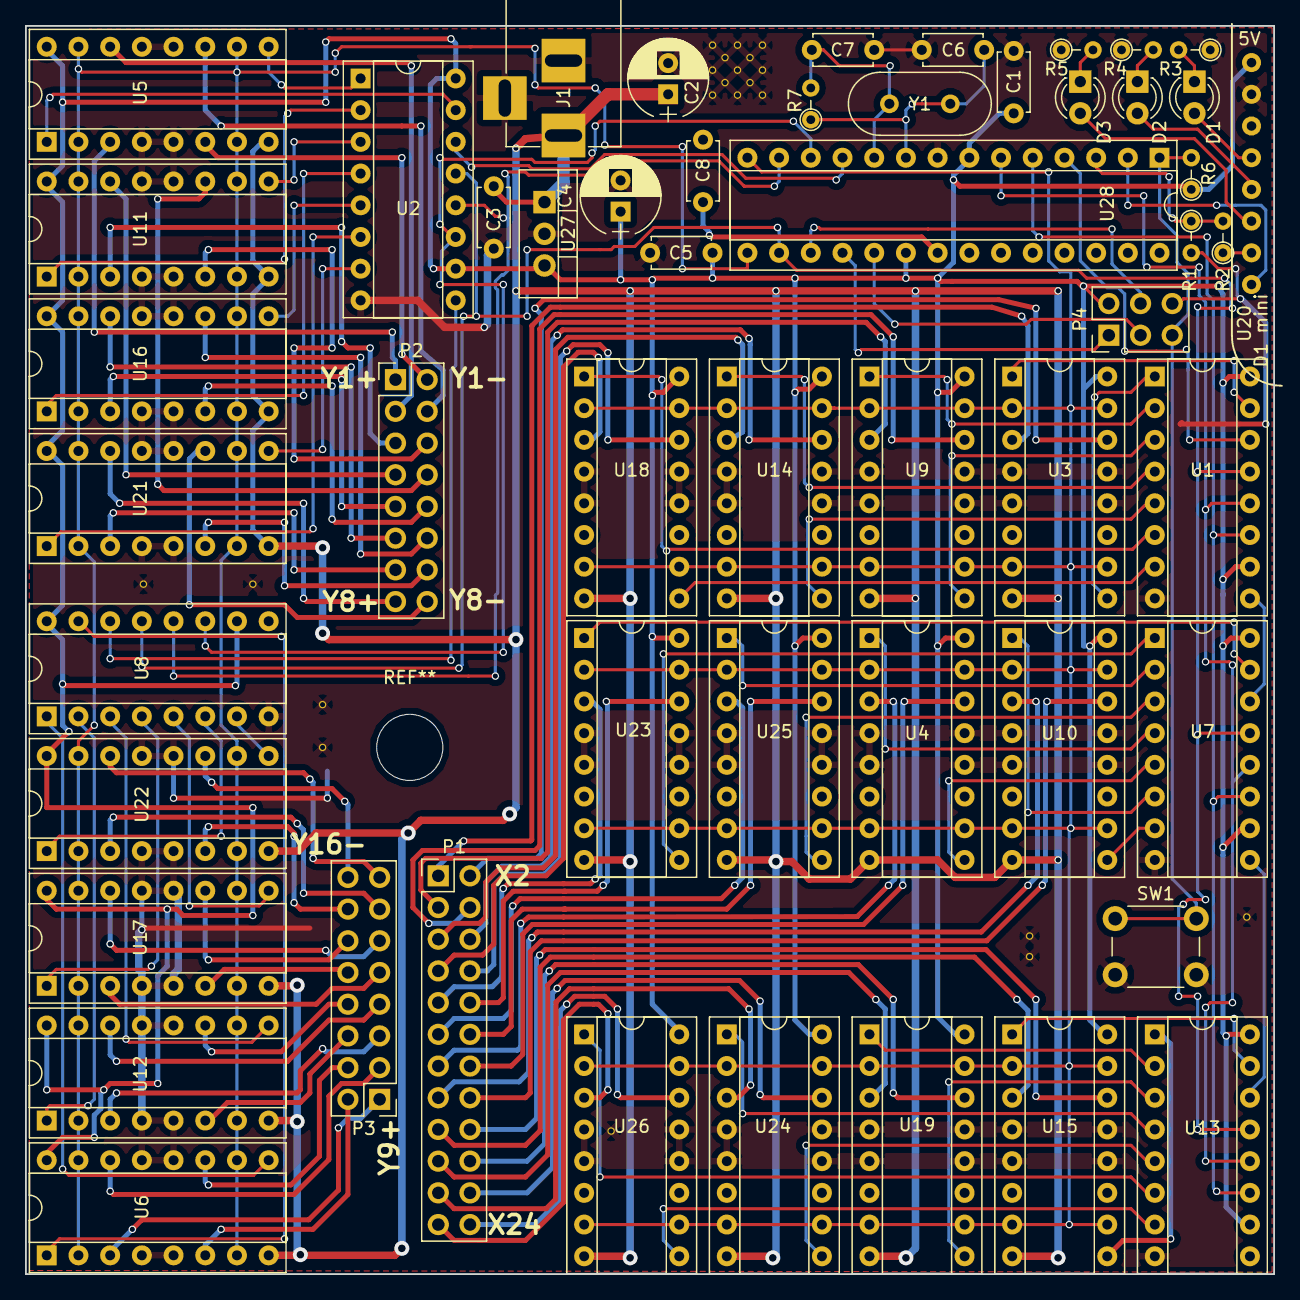
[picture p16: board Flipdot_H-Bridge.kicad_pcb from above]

Board: 2 copper layers, 100.0 x 100.0 mm, 53 parts (0 on the bottom side), 127 nets.

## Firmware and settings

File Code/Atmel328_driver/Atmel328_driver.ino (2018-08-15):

/*
 * FlipDotDisplay Atmel328 Firmware
 * 
 * This is the software for the display controller of the FlipDotDisplay. It handles the 
 * management of the shift registers and H-bridge drivers. The communication between this 
 * controller and the ESP8266 is done via serial communication with an 8bit header and a
 * checksum byte.
 * 
 * 
 * by Patrick Kübler (2018)
 * License: Creative Commons 4.0
 */



//number of dots in X and Y 
//(For multidisplay: enter size of total display)
const int sizeX = 24;
const int sizeY = 48;

//multidisplay position
const int multi = 2; // first  =^ 0
const int multiSize = 3;// displays in Y

// Shift register pins
const int pin_Shift_Data_X = 2;   
const int pin_Shift_Clock_X = 3;
const int pin_Shift_Latch_X = 4;

const int pin_Shift_Data_Y = 5;
const int pin_Shift_Clock_Y = 6;
const int pin_Shift_Latch_Y = 7;

// enables output of shift registers, active = LOW
const int OE = 10;

// sets output of the half-briges 
// LOW = GND
// HIGH = VIN
const int pin_Data_X = 8;
const int pin_Data_Y = 9;

// pulse length of a bit flip
// in µSec
const int time_Flip = 800;


// Serial protocol
// ===============
const uint8_t serial_header = 0xaa;
const uint8_t dataSize = (sizeX * sizeY/multiSize )/8;
//header+payload+checksum
const int bufferSize = (dataSize*multiSize) + 2;

uint8_t dataBuffer[bufferSize];
uint8_t readCounter = 0;
bool isHeader = false;
bool firstTimeHeader = false;

// array for storing the current display 
byte currentData[dataSize] = { 0 };

void setup() {
  Serial.begin(115200);
  
  pinMode(OE, OUTPUT);
  digitalWrite(OE, LOW);
  
  pinMode(pin_Shift_Data_X, OUTPUT);
  pinMode(pin_Shift_Clock_X, OUTPUT);
  pinMode(pin_Shift_Latch_X, OUTPUT);

  pinMode(pin_Shift_Data_Y, OUTPUT);
  pinMode(pin_Shift_Clock_Y, OUTPUT);
  pinMode(pin_Shift_Latch_Y, OUTPUT);

  pinMode(pin_Data_X, OUTPUT);
  pinMode(pin_Data_Y, OUTPUT);

  // wipe display
  clearAll();
}

void loop() {

  if( Serial.available() ){
    //Serial.println("reciving Data");
    readData();
  }
  //delay(1000);
  //Serial.print("dataSize= ");
  //Serial.println(dataSize);
}
    

void clearAll(){
  for( int i = 0; i<(sizeX*sizeY); i++ ){
    writeFlip(i%sizeX,
              i/sizeX,
              LOW);
  }
  for( int i = 0; i < dataSize; i++ ){
    currentData[i] = B00000000;
  }
}

void readData() {
  // get first byte from Serial buffer
  uint8_t c = Serial.read();
  
  if ( c == serial_header ) {
    if( !firstTimeHeader ) {
      isHeader = true;
      readCounter = 0;
      firstTimeHeader = true;
    }
  }
  
  dataBuffer[readCounter] = c;
  readCounter++;
  
  if( readCounter >= (bufferSize) ) {

    readCounter = 0;
    
    if( isHeader ) {
      uint8_t checksumByte = dataBuffer[bufferSize-1];
    
      if( checksum(checksumByte) ) {
        
        // Transfer buffer into display data
        byte data[dataSize];

        for( int i = 0; i < dataSize; i++ ){
          data[i] = dataBuffer[i+1 + (dataSize*multi)];
        }

        writeData(data);
      }
      else{
        Serial.println("Error");
      }
      
      // restart header flag
      isHeader = false;
      firstTimeHeader = false;
    }
  }
}

bool checksum(byte checksumValue) {
  //return true;
  byte result = 0;
  uint16_t sum = 0;
  
  for( int i = 0; i < (bufferSize-1); i++ ) {
    sum += dataBuffer[i];
  }
  result = sum & 0xFF;
  
  if(checksumValue == result ) {
     return true;
  }
  else {
     return false;
  }
}

void writeData(byte data[]) {

  Serial.println("Writing Display");
  for( int i=0; i<dataSize; i++ ){ 
    for( int j=0; j<8; j++ ){
      // compare current dot with new one
      if( bitRead(data[i], 7-j) != bitRead(currentData[i], 7-j) ){
        writeFlip( ( (i*8) + j) % sizeX,
                   ( (i*8) + j) / sizeX,
                   bitRead(data[i], 7-j)
                  );
      }
    }
  }
  // save new dislay data
  memcpy(currentData, 
         data,
         sizeof(currentData)*sizeof(byte));
}

void writeFlip(uint8_t cooX, uint8_t cooY, bool flip) {
  
  pushCoordinate(cooX,cooY);

  if( flip ){
    digitalWrite(pin_Data_Y, HIGH);
    delayMicroseconds(time_Flip);
    digitalWrite(pin_Data_Y, LOW);
  }
  else {
    digitalWrite(pin_Data_X, HIGH);
    delayMicroseconds(time_Flip);
    digitalWrite(pin_Data_X, LOW);
  }
}

void pushCoordinate(uint8_t cooX, uint8_t cooY) {
  /*
      0 1 2 3 4 5 6 7 …
    0
    1
    2   X
    3
    4
    5
    6
    7
    …
  */
  //coordianates start at 0

  // push Y coordinates in reverse order
  // so if dot 0x0 is flipped the high bit
  // is pushed in last

  // Y-Axis
  for( int i = 0; i < sizeY; i++ ){
    
    if ( i == ( (sizeY-1) - cooY) ){
      pushDataY(HIGH);
    }
    else {
      pushDataY(LOW);
    }
  }

  // X-Axis
  for( int i = 0; i < sizeX; i++ ){
    if(i == ( (sizeX-1) - cooX ) ){
      pushDataX(HIGH);
    }
    else {
      pushDataX(LOW);
    }
  }

  //move the data to the output registers
  digitalWrite(pin_Shift_Latch_X, HIGH);
  digitalWrite(pin_Shift_Latch_X, LOW);

  digitalWrite(pin_Shift_Latch_Y, HIGH);
  digitalWrite(pin_Shift_Latch_Y, LOW);
}

void pushDataX(bool state) {
  // pushes a new bit into the shift registers
  // digitalWrite() delay is long enough to trigger the clock
  
  digitalWrite(pin_Shift_Data_X, state);
  digitalWrite(pin_Shift_Clock_X, HIGH);
  digitalWrite(pin_Shift_Clock_X, LOW);
  // latching needs to be done in the pushCoordinates function
}

void pushDataY(bool state) {
  // pushes a new bit into the shift registers
  // digitalWrite() delay is long enough to trigger the clock
  
  digitalWrite(pin_Shift_Data_Y, state);
  digitalWrite(pin_Shift_Clock_Y, HIGH);
  digitalWrite(pin_Shift_Clock_Y, LOW);
  // latching needs to be done in the pushCoordinates function
}

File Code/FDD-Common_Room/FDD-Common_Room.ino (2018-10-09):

/*
 * Program running on the FlipDotDisplay
 * in the CoMakingSpace Common Room.
 * 
 * Functions
 * - Display Time via NTP
 * - Text scroll via MQTT trigger
 * - Display Binary via MQTT (kind of works, but not really well)
 *   - one needs to increase the character limit of the Adafruit MQTT library to 144+
 * 
 * by Patrick Kübler
 * License: Creative Commons 4.0
 */

#include "Arduino.h"
#include "Adafruit_GFX.h"
#include "FlipDotDisplay.h"
#include <ArduinoOTA.h>
#include <ESP8266WiFi.h>
#include <WiFiUdp.h>
#include <Adafruit_MQTT.h>
#include <Adafruit_MQTT_Client.h>
#include <NTPClient.h>
#include <TaskScheduler.h>
#include "Passwords.h"
WiFiUDP ntpUDP;
NTPClient timeClient(ntpUDP, "0.de.pool.ntp.org", 7200, 600000);

#define AIO_SERVER      "comakingcontroller"
#define AIO_SERVERPORT  1883

WiFiClient client;

Adafruit_MQTT_Client  mqtt(&client, AIO_SERVER, AIO_SERVERPORT);

Adafruit_MQTT_Subscribe textTopic = Adafruit_MQTT_Subscribe(&mqtt, "/CommonRoom/FDD/Text");
Adafruit_MQTT_Subscribe binaryTopic = Adafruit_MQTT_Subscribe(&mqtt, "/CommonRoom/FDD/Binary");



// initialize display with 24x16 dots
FlipDotDisplay flip(48,24);

void displayTime();
void MQTT_update();

void binaryData(char* data, uint16_t length){
  flip.clear();
  
  uint8_t tempArray[144] = {0};
  
  for (int i = 0; i < length; i++){
    tempArray[i] = data[i];
  }
  
  flip.writeData(tempArray);
  delay(1000);
}

void textData(char* data, uint16_t length){
  scrollText((String)data);
}

// refresh display to avoid stuck dots
void refresh() {
  uint8_t tempArray[144];
  for (int i = 0; i < 144; i++){
    tempArray[i] = 0xFF;
  }
  
  flip.clear();
  flip.display();
  delay(100);
  
  flip.writeData(tempArray);
  flip.display();
  delay(100);
  
  flip.clear();
  flip.display();
  
  /*
  for (int y = 23; y >= 0; y--) {    
    for (int x = 0; x < 48; x++) {
      flip.clear();
      flip.drawPixel(x,y,1);
      flip.display();
      delay(5);
      flip.drawPixel(x,y,0);
      flip.display();
      delay(5);
    } 
  }
  */
}


// ### Task Scheduler ###
Task timeTask(1000, TASK_FOREVER, &displayTime);
Task MQTTTask(1000, TASK_FOREVER, &MQTT_update);
Task refreshTask(3600000, TASK_FOREVER, &refresh);

Scheduler runner;

void setup() {
  Serial.println("Booting");
  flip.print("Booting...");
  flip.display();

// ### WiFi Setup ####
  
  WiFi.mode(WIFI_STA);

  WiFi.hostname("FlipDotDisplay");
  WiFi.begin(ssid, password);
  while (WiFi.waitForConnectResult() != WL_CONNECTED) {
    Serial.println("Connection Failed! Rebooting...");
    delay(5000);
    ESP.restart();
  }


// ### OTA Setup ####
  ArduinoOTA.setHostname("FlipDotDisplay");

  // Port defaults to 8266
  // ArduinoOTA.setPort(8266);

  // Hostname defaults to esp8266-[ChipID]


  //No authentication by default
  ArduinoOTA.setPassword(OTA_password);

  // Password can be set with it's md5 value as well
  // MD5(admin) = 21232f297a57a5a743894a0e4a801fc3
  // ArduinoOTA.setPasswordHash("21232f297a57a5a743894a0e4a801fc3");

  ArduinoOTA.onStart([]() {
    String type;
    if (ArduinoOTA.getCommand() == U_FLASH) {
      type = "sketch";
    } else { // U_SPIFFS
      type = "filesystem";
    }

    // NOTE: if updating SPIFFS this would be the place to unmount SPIFFS using SPIFFS.end()
    Serial.println("Start updating " + type);
  });
  ArduinoOTA.onEnd([]() {
    Serial.println("\nEnd");
  });
  ArduinoOTA.onProgress([](unsigned int progress, unsigned int total) {
    Serial.printf("Progress: %u%%\r", (progress / (total / 100)));
  });
  ArduinoOTA.onError([](ota_error_t error) {
    Serial.printf("Error[%u]: ", error);
    if (error == OTA_AUTH_ERROR) {
      Serial.println("Auth Failed");
    } else if (error == OTA_BEGIN_ERROR) {
      Serial.println("Begin Failed");
    } else if (error == OTA_CONNECT_ERROR) {
      Serial.println("Connect Failed");
    } else if (error == OTA_RECEIVE_ERROR) {
      Serial.println("Receive Failed");
    } else if (error == OTA_END_ERROR) {
      Serial.println("End Failed");
    }
  });
  ArduinoOTA.begin();
  Serial.println("Ready");
  Serial.print("IP address: ");
  Serial.println(WiFi.localIP());
  
  flip.setTextWrap(false);


// ### MQTT Setup ###
  binaryTopic.setCallback(binaryData);
  textTopic.setCallback(textData);

  mqtt.subscribe(&textTopic);
  mqtt.subscribe(&binaryTopic);

// ### Initialize Tasks ###
  runner.init();
  runner.addTask(timeTask);
  runner.addTask(MQTTTask);
  runner.addTask(refreshTask);
  timeTask.enable();
  MQTTTask.enable();
  refreshTask.enable();
}

void loop() {
  
  ArduinoOTA.handle();
  
  runner.execute();

}

void MQTT_update(){
  MQTT_connect();
  mqtt.processPackets(1000);
//  Adafruit_MQTT_Subscribe *subscription;
//  while ((subscription = mqtt.readSubscription(1000))) {
//   
//    if (subscription == &textTopic) {
//      char* text = (char*)textTopic.lastread;
//      String textToDisplay =  (String)text;
//      scrollText(textToDisplay);
//    }
//    if (subscription == &binaryTopic) {
//      //Theoretically, the MQTT library returns the data as uint8_t
//      //Therefore, just passing it to the writeData function should work.
//      //However, this was not yet tested
//      //Especially the boundaries of the Adafruit library (SUBSCRIPTIONDATALEN) might have to be adjusted
//      //flip.clear();
//      //flip.writeData(binaryTopic.lastread);
//      //delay(150);
//    }
//  }
}
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

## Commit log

2017-09-03 moved files
    [ATM_Driver.sch, Arduino.sch, FlipDotWiring.sch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]
2017-09-05 routing of H-bridge traces
    [ATM_Driver.sch, Flipdot_H-Bridge.sch]
2017-09-05 added plots of the schematic
2018-02-21 finished layout V1
    [Flipdot_H-Bridge.kicad_pcb, _saved_ATM_Driver.sch, _saved_Flipdot_H-Bridge.sch]
2018-02-21 gernerated Gerber and drill files in plot/
    [ATM_Driver.sch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]
2018-02-21 updated schematic plots plots
    [Flipdot_H-Bridge.sch]
2018-04-25 labeled triac design as depricated
    [Arduino.sch, FlipDotWiring.sch, FlipDot_Circuit.kicad_pcb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]
2018-04-25 PCB V1
    [Arduino.sch, FlipDotWiring.sch, FlipDot_Circuit.kicad_pcb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]
2018-04-25 removed dead files
    [Schematics_H-Bridge.kicad_pcb, Schematics_H-Bridge.sch]
2018-04-25 PCB v1.1, minor fixes in connector and silkscreen layout
    [Flipdot_H-Bridge-B.Cu.gbr, Flipdot_H-Bridge-B.Mask.gbr, Flipdot_H-Bridge-B.SilkS.gbr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]
2018-04-25 removed old ESP code
    [Flipdot_H-Bridge-B.Cu.gbr, Flipdot_H-Bridge-B.Mask.gbr, Flipdot_H-Bridge-B.SilkS.gbr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]
2018-04-25 PNG version of wiring
2018-04-25 removed double triac design
    [Arduino.sch, FlipDotWiring.sch, FlipDot_Circuit.kicad_pcb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]
2018-05-22 removed duplicated ESP folder and moved Atmel driver sketch into its own folder
2018-08-15 updated driver to allow for MultiDisplay use
2018-09-07 removed binary handling as it causes the ESP to crash
    [FDD-Common_Room.ino]
2018-09-07 fixed special character display
    [FDD-Common_Room.ino]
2018-10-09 added an hourly display refresh to reset dead pixels
    [FDD-Common_Room.ino]
